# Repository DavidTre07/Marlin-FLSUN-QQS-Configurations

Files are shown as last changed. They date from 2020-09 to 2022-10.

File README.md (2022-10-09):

# 1. Marlin configuration files for FLSUN QQ-S

- [1. Marlin configuration files for FLSUN QQ-S](#1-marlin-configuration-files-for-flsun-qq-s)
  - [1.1. Purpose of this git](#11-purpose-of-this-git)
  - [1.2. How to use these files](#12-how-to-use-these-files)
  - [1.3. How to Flash](#13-how-to-flash)
  - [1.4. 1st startup after flashing a new firmware](#14-1st-startup-after-flashing-a-new-firmware)
  - [1.5. Hot End PID Tune](#15-hot-end-pid-tune)
  - [1.6. Bed PID Tune](#16-bed-pid-tune)
  - [1.7. Calibrate extruder E-Step](#17-calibrate-extruder-e-step)
  - [1.8. Level the bed](#18-level-the-bed)
  - [1.9. Calibrate dimensional print](#19-calibrate-dimensional-print)
  - [1.10. Temperature tower](#110-temperature-tower)
  - [1.11. References / Usefull Links](#111-references--usefull-links)

---

## 1.1. Purpose of this git

This is a repository for FLSUN QQ-S Marlin configuration files,  
The printer is a stock one (without mods).  
You will find also in this readme some How To for configuring / tuning your delta printer.  

---

## 1.2. How to use these files

1. Download Marlin source code (<https://marlinfw.org/>)  
2. Extract Zip file
3. Copy this repository files in the extracted Marlin zip folder  
4. Start VSCODE, install PlatformIO plugin  
5. Point VSCODE to Marlin folder  
6. Compile it !  

---

## 1.3. How to Flash

1. When compiled, copy .pio\build\mks_robin_mini\Robin_mini.bin on a MicroSD card  
2. Power off the printer
3. Insert MicroSD in the printer  
4. Power on the printer  
5. Printer will tell you the upgrade is in progress  

---

## 1.4. 1st startup after flashing a new firmware

1. Init EEPROM [*Configuration->Advanced Settings->Initialize EEPROM*]  
2. Mount the magnetic leveling switch  
3. Start Delta auto Calibration (Very long...) [*Configuration->Delta Calibration->Auto Calibration*]  
4. Heat up the hotend + Bed
5. Start Bed leveling [*Motion->Level Bed*]  
6. Now remove leveling switch  
7. Move Head to Z=0 (Be carefull, normally it will not touch the bed but you have to verify during the move)  
8. Configure Z probe offset with the paper test [*Configuration->Probe Z offset*]  
9. Save configuration in EEPROM [*Configuration->Store settings*]

---

## 1.5. Hot End PID Tune

For the following procedure I used Octoprint terminal tab:  

1. Start fan at max speed: **M106 S255**  
2. Execute auto-PID: **M303 E0 S200 C8**  
   Explanation: Hotend 0, Temp 200, 8 times  
3. Actual Firmware configuration: M301 P28.16 I3.38 D58.69  
   New value found : **M301 P16.90 I0.94 D75.85**  
   :warning: Warning: I installed a silicon protection around the heating block so don't use these values for your printer.
4. Save with : **M500**

---

## 1.6. Bed PID Tune

For the following procedure use Octoprint terminal tab:  

1. Execute auto-PID: **M303 E-1 S60 C8**  
   Explanation: Bed, Temp 60, 8 times  
2. Actual Firmware configuration: M304 P325.10 I63.35 D417.10  
   New value found: **M304 P79.68 I15.29 D276.77**
3. Save with: **M500**

---

## 1.7. Calibrate extruder E-Step

For the following procedure use Octoprint terminal tab:  

1. Remove the bowden on the extruder motor
2. Allow cold extrusion: **M302 P1**
3. Relative mode: **M83**
4. Extrude 30 cm at 500mm/min: **G1 E300 F500**
5. Check if the length is 30 cm
6. If not OK:
   - Check the current steps/mm: **M92** (Only the E value will be changed)
   - Calculate new E-Steps: *CurrentValue\*300/MesuredLength*
   - Configure the new steps/mm: **M92 E391**
   - Restart from step 3.
7. If OK then disallow cold extrusion: **M302 P0**
8. Save new value: **M500**

---

## 1.8. Level the bed

Start to check if there is a mesh, if not it will start to create a new one: **G29 V1**
Activate bed leveling : **M420 S1**
Save configuration : **M500**
Don't forget to configure you slicer to include a **M420 S1** just after **G28**

---

## 1.9. Calibrate dimensional print

Print a dice of the size of your choice.  You can found some in the stl folder.  
Recommended values of your slicer: 5% filling, speed 40mm/s.  
When done use a caliper to verify the dice size.  

If you face a difference in the size you have to adjust diagonal rod size:  

1. Print the curent configuration with: **M503**  
   Look for:  

   ```text
   Delta settings: L<diagonal rod> R<radius> H<height> S<segments per sec> XYZ<tower angle trim> ABC<rod trim>  
   M665 L280.00 R141.86 H359.31 S200.00 X-0.44 Y0.62 Z-0.18 A0.00 B0.00 C0.00
   ```

   You have to adjust *L\<diagonal rod\>*

2. Calculate the new value:  
For example if you printed a 100 mm dice but you find 99.8 mm:  
calculate the new value: *CurrentValue\*IdealSize/MesuredSize*  (280*100/99.8=280.56)  

3. Configure the new value: **M665 L280.56**

4. As you modfied the Diagonal Rod size, you have to redo:
   - Delta auto Calibration: **G33**  
   - Hot end and bed heating: **M104 S200** + **M190 S60**
   - Bed leveling: **G29**
   - Probe Z offset (paper test)
   - End of hot end and bed heating: **M104 S0; M140 S0**

Delta auto calibration + Bed leveling + ... take long time, so:

- print slowly the dice
- a small dice is nice because it print in a short time but a big dice would provide you better accuracy  
  I use a 1 cm dice for the first try then  
  2 cm dice for next adjustement  
  and finally a last 10 cm dice when close a final config (very long but accurate)  
- pay attention of the mesured size of your dice  
  (for example the first layer is usually larger so try to make mesurement without the first layer)  

---

## 1.10. Temperature tower

> TO WRITE

---

## 1.11. References / Usefull Links

|||
|:----|:---|
|Facebook group|<https://www.facebook.com/groups/120961628750040/>|
|Anders Sahlman Github|<https://github.com/AndersSahlman/Marlin>|
|Interresting Anders' post|<https://www.facebook.com/groups/120961628750040/permalink/593987384780793/>|
|Flsun QQ/QQS FAQ|<https://docs.google.com/document/d/1b_2N7NpQN2e96VPfVc_poLPOWwkM93tdAHZWOD4WEw8/edit?usp=sharing>|
|WIFI upgrade|<https://www.facebook.com/groups/120961628750040/?post_id=623723315140533><BR><https://github.com/luc-github/ESP3D>|
|Extruder calibration|<https://mattshub.com/blog/2017/04/19/extruder-calibration>|
|Calibration Hexagon|<https://www.thingiverse.com/thing:1274733>|
|Calibration Dice|<https://github.com/DavidTre07/Marlin-FLSUN-QQS-Configurations/tree/master/stl/Cube>|
|Parts for FLSUN QQS|<https://www.thingiverse.com/thing:4206957>|
|||

To Test:
|||
|:-|:-|
|Octopi Delta Micro Calibration|<https://plugins.octoprint.org/plugins/DuCalibrator>|
|||

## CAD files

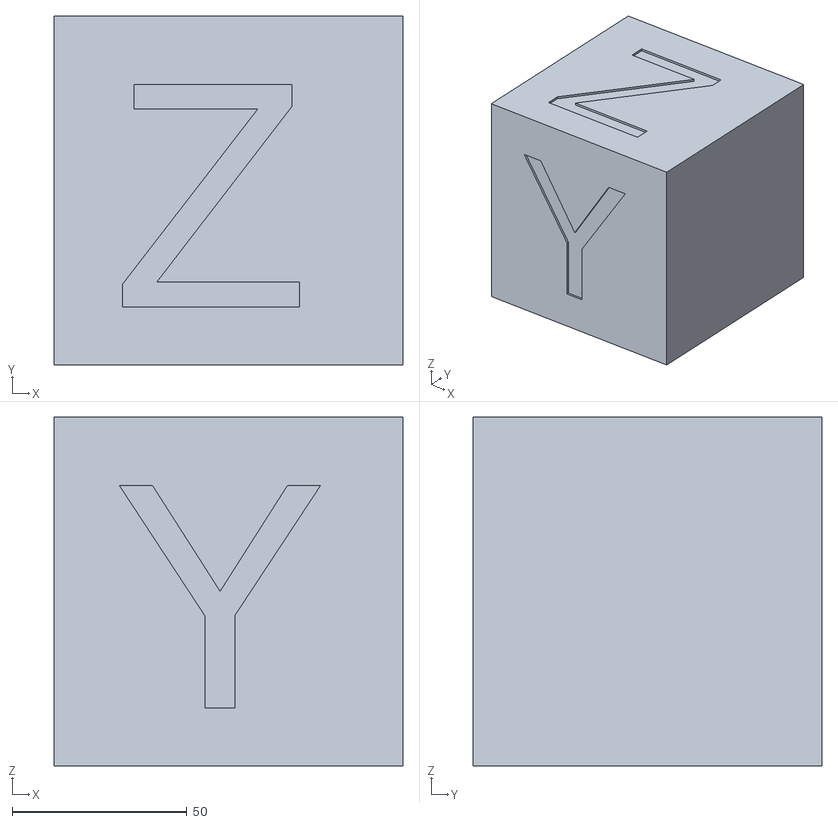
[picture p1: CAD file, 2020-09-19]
stl/Cube/100mm Calibration Cube.STL
100.0 x 100.0 x 100.0

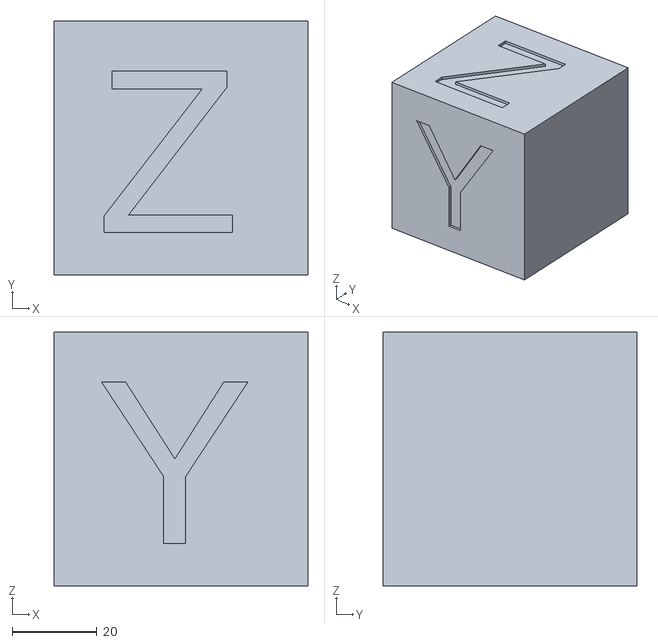
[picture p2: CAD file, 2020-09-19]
stl/Cube/60mm Calibration Cube.STL
60.0 x 60.0 x 60.0

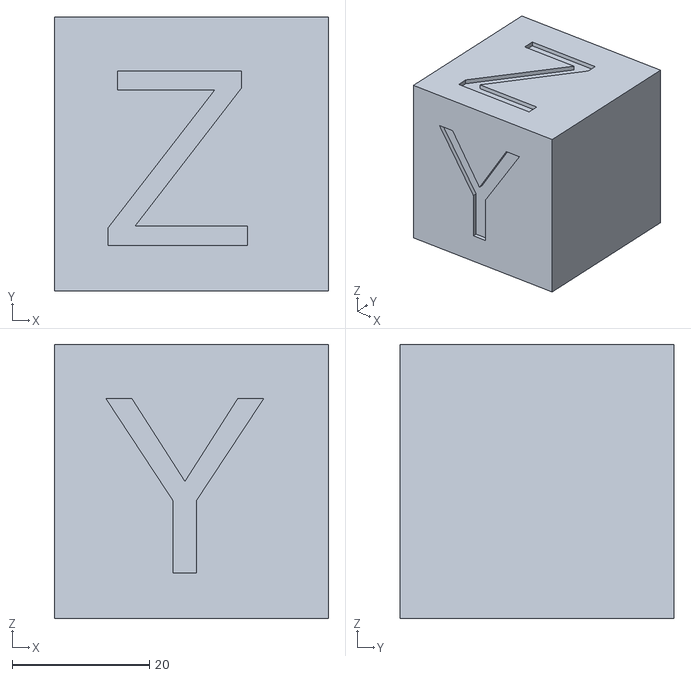
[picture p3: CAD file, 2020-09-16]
stl/Cube/40mm Calibration Cube.STL
40.0 x 40.0 x 40.0

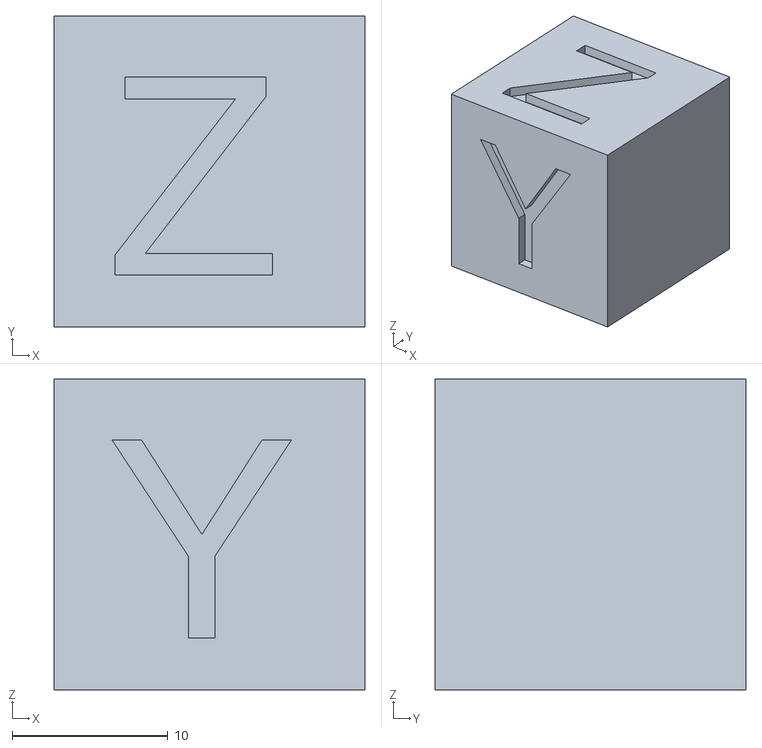
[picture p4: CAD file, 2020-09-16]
stl/Cube/20mm Calibration Cube.STL
20.0 x 20.0 x 20.0

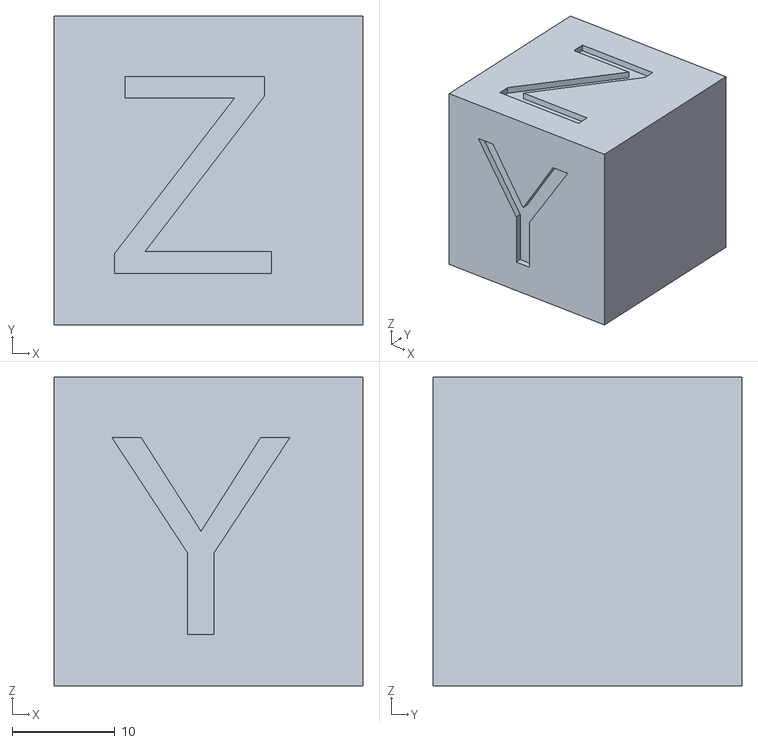
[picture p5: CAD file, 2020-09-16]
stl/Cube/30mm Calibration Cube.STL
30.0 x 30.0 x 30.0

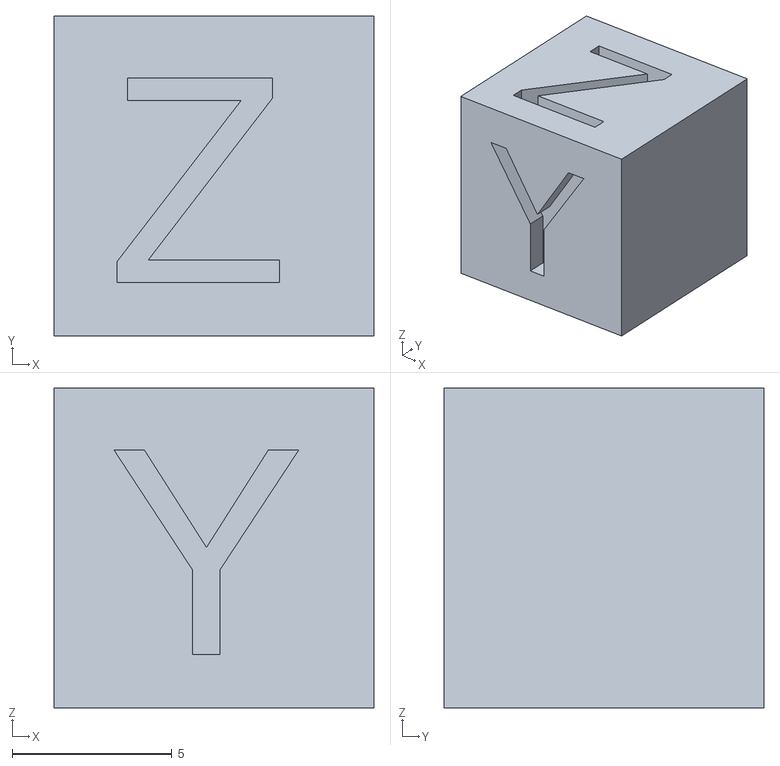
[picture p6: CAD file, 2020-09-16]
stl/Cube/10mm Calibration Cube.STL
10.0 x 10.0 x 10.0

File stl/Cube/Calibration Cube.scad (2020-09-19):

//http://github.com/DavidTre07
//Dice size in mm
size=60;

//Do not modify under this line
letterSize=size/1.5;
letterThin=1;
$fn=300;
epsilon=0.01;

difference(){
   cube(size=size);
   translate([-epsilon,(size-letterSize)/2,(size-letterSize)/2])rotate([90,0,90])
      linear_extrude(height=letterThin)text("X",size=letterSize);
   translate([(size-letterSize)/2,letterThin-epsilon,(size-letterSize)/2])rotate([90,0,0])
      linear_extrude(height=letterThin)text("Y",size=letterSize);
   translate([(size-letterSize)/2,(size-letterSize)/2,size-letterThin+epsilon])rotate([0,0,0])
      linear_extrude(height=letterThin)text("Z",size=letterSize);
}

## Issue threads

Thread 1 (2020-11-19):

Reverse display

mayalex, 2020-11-19:
Hello @DavidTre07! Perhaps, can you help me?
I used your config and got reverse display, but a touch works without reverse. (Stock Printer 2019 QQ-S)
Have been this experience?
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

Thanks!

DavidTre07, 2020-11-19:
Hello @mayalex , I don't know how to solve this issue.
I remember a old commit form Anders Sahlman on his repo about this problem but I don't know if it has been merged in Marlin.
You can check here: https://github.com/AndersSahlman/Marlin/commit/7eed139608c5388aa849a639d0142308d55b37ee
Perhaps he can drive you in the right direction.

Sorry not be very helpfull !

mayalex, 2020-11-20:
Hello @DavidTre07!
Thanks)
I solved this problem, added TFT_ROTATION with value:
`#define TFT_ROTATION TFT_ROTATE_180_MIRROR_Y`
`#define TFT_ROTATION TFT_ROTATE_180_MIRROR_X`

Closed 2020-11-20.

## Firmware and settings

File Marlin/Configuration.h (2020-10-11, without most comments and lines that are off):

#pragma once
#define CONFIG_EXAMPLES_DIR "delta/FLSUN/QQ-S"
#define CONFIGURATION_H_VERSION 020007
#define STRING_CONFIG_H_AUTHOR "(DavidTre, QQ-S config)" // Who made the changes.
#define SHOW_BOOTSCREEN
#define SERIAL_PORT 3
#define SERIAL_PORT_2 1
#define BAUDRATE 250000
  #define MOTHERBOARD BOARD_MKS_ROBIN_MINI
#define CUSTOM_MACHINE_NAME "FLSUN QQ-S"
#define EXTRUDERS 1
#define DEFAULT_NOMINAL_FILAMENT_DIA 1.75
#define TEMP_SENSOR_0 1
#define TEMP_SENSOR_1 0
#define TEMP_SENSOR_2 0
#define TEMP_SENSOR_3 0
#define TEMP_SENSOR_4 0
#define TEMP_SENSOR_5 0
#define TEMP_SENSOR_6 0
#define TEMP_SENSOR_7 0
#define TEMP_SENSOR_BED 1
#define TEMP_SENSOR_PROBE 0
#define TEMP_SENSOR_CHAMBER 0
#define DUMMY_THERMISTOR_998_VALUE 25
#define DUMMY_THERMISTOR_999_VALUE 100
#define MAX_REDUNDANT_TEMP_SENSOR_DIFF 10
#define TEMP_RESIDENCY_TIME     10  // (seconds) Time to wait for hotend to "settle" in M109
#define TEMP_WINDOW              1  // (°C) Temperature proximity for the "temperature reached" timer
#define TEMP_HYSTERESIS          3  // (°C) Temperature proximity considered "close enough" to the target
#define TEMP_BED_RESIDENCY_TIME  10 // (seconds) Time to wait for bed to "settle" in M190
#define TEMP_BED_WINDOW          1  // (°C) Temperature proximity for the "temperature reached" timer
#define TEMP_BED_HYSTERESIS      3  // (°C) Temperature proximity considered "close enough" to the target
#define HEATER_0_MINTEMP   5
#define HEATER_1_MINTEMP   5
#define HEATER_2_MINTEMP   5
#define HEATER_3_MINTEMP   5
#define HEATER_4_MINTEMP   5
#define HEATER_5_MINTEMP   5
#define HEATER_6_MINTEMP   5
#define HEATER_7_MINTEMP   5
#define BED_MINTEMP        5
#define HEATER_0_MAXTEMP 275
#define HEATER_1_MAXTEMP 275
#define HEATER_2_MAXTEMP 275
#define HEATER_3_MAXTEMP 275
#define HEATER_4_MAXTEMP 275
#define HEATER_5_MAXTEMP 275
#define HEATER_6_MAXTEMP 275
#define HEATER_7_MAXTEMP 275
#define BED_MAXTEMP      110
#define PIDTEMP
#define BANG_MAX 255     // Limits current to nozzle while in bang-bang mode; 255=full current
#define PID_MAX BANG_MAX // Limits current to nozzle while PID is active (see PID_FUNCTIONAL_RANGE below); 255=full current
#define PID_K1 0.95      // Smoothing factor within any PID loop
  #define PID_EDIT_MENU         // Add PID editing to the "Advanced Settings" menu. (~700 bytes of PROGMEM)
  #define PID_AUTOTUNE_MENU     // Add PID auto-tuning to the "Advanced Settings" menu. (~250 bytes of PROGMEM)
    #define DEFAULT_Kp  16.90
    #define DEFAULT_Ki   0.94
    #define DEFAULT_Kd  75.85
#define PIDTEMPBED
#define MAX_BED_POWER 255 // limits duty cycle to bed; 255=full current
  #define DEFAULT_bedKp 79.68
  #define DEFAULT_bedKi 15.29
  #define DEFAULT_bedKd 276.77
  #define PID_FUNCTIONAL_RANGE 15 // If the temperature difference between the target temperature and the actual temperature
#define PREVENT_COLD_EXTRUSION
#define EXTRUDE_MINTEMP 170
#define PREVENT_LENGTHY_EXTRUDE
#define EXTRUDE_MAXLENGTH 950
#define THERMAL_PROTECTION_HOTENDS // Enable thermal protection for all extruders
#define THERMAL_PROTECTION_BED     // Enable thermal protection for the heated bed
#define DELTA
  #define DELTA_SEGMENTS_PER_SECOND 200
  #define DELTA_HOME_TO_SAFE_ZONE
  #define DELTA_CALIBRATION_MENU
  #define DELTA_AUTO_CALIBRATION
    #define DELTA_CALIBRATION_DEFAULT_POINTS 7
    #define PROBE_MANUALLY_STEP 0.05      // (mm)
  #define DELTA_PRINTABLE_RADIUS 130.0    // (mm)
  #define DELTA_DIAGONAL_ROD 280.0        // (mm)
  #define DELTA_HEIGHT 372.00             // (mm) Get this value from G33 auto calibrate
  #define DELTA_ENDSTOP_ADJ { 0.0, 0.0, 0.0 } // Get these values from G33 auto calibrate
  #define DELTA_RADIUS 140.8              // (mm) Get this value from G33 auto calibrate
  #define DELTA_TOWER_ANGLE_TRIM { 0.0, 0.0, 0.0 } // Get these values from G33 auto calibrate
  #define DELTA_DIAGONAL_ROD_TRIM_TOWER { 0.0, 0.0, 0.0 }
#define USE_ZMIN_PLUG // a Z probe
#define USE_XMAX_PLUG
#define USE_YMAX_PLUG
#define USE_ZMAX_PLUG
#define ENDSTOPPULLUPS
#define X_MIN_ENDSTOP_INVERTING false  // Set to true to invert the logic of the endstop.
#define Y_MIN_ENDSTOP_INVERTING false  // Set to true to invert the logic of the endstop.
#define Z_MIN_ENDSTOP_INVERTING true  // Set to true to invert the logic of the endstop.
#define X_MAX_ENDSTOP_INVERTING false  // Set to true to invert the logic of the endstop.
#define Y_MAX_ENDSTOP_INVERTING false  // Set to true to invert the logic of the endstop.
#define Z_MAX_ENDSTOP_INVERTING false  // Set to true to invert the logic of the endstop.
#define Z_MIN_PROBE_ENDSTOP_INVERTING true  // Set to true to invert the logic of the probe.
#define X_DRIVER_TYPE  A4988
#define Y_DRIVER_TYPE  A4988
#define Z_DRIVER_TYPE  A4988
#define E0_DRIVER_TYPE A4988
#define XYZ_FULL_STEPS_PER_ROTATION 200
#define XYZ_MICROSTEPS 16
#define XYZ_BELT_PITCH 2
#define XYZ_PULLEY_TEETH 16
#define DEFAULT_XYZ_STEPS_PER_UNIT ((XYZ_FULL_STEPS_PER_ROTATION) * (XYZ_MICROSTEPS) / double(XYZ_BELT_PITCH) / double(XYZ_PULLEY_TEETH))
#define DEFAULT_AXIS_STEPS_PER_UNIT   { DEFAULT_XYZ_STEPS_PER_UNIT, DEFAULT_XYZ_STEPS_PER_UNIT, DEFAULT_XYZ_STEPS_PER_UNIT, 393 }  // default steps per unit
#define DEFAULT_MAX_FEEDRATE          { 200, 200, 200, 200 }
#define DEFAULT_MAX_ACCELERATION      { 1000, 1000, 1000, 1000 }
#define LIMITED_MAX_ACCEL_EDITING     // Limit edit via M201 or LCD to DEFAULT_MAX_ACCELERATION * 2
  #define MAX_ACCEL_EDIT_VALUES       { 6000, 6000, 6000, 20000 } // ...or, set your own edit limits
#define DEFAULT_ACCELERATION          1000    // X, Y, Z and E acceleration for printing moves
#define DEFAULT_RETRACT_ACCELERATION  1000    // E acceleration for retracts
#define DEFAULT_TRAVEL_ACCELERATION   1000    // X, Y, Z acceleration for travel (non printing) moves
#define CLASSIC_JERK
  #define DEFAULT_XJERK 10.0
  #define DEFAULT_YJERK DEFAULT_XJERK
  #define DEFAULT_ZJERK DEFAULT_XJERK // Must be same as XY for delta
  #define LIMITED_JERK_EDITING        // Limit edit via M205 or LCD to DEFAULT_aJERK * 2
    #define MAX_JERK_EDIT_VALUES { 20, 20, 20, 10 } // ...or, set your own edit limits
#define DEFAULT_EJERK    5.0  // May be used by Linear Advance
#define S_CURVE_ACCELERATION
#define Z_MIN_PROBE_USES_Z_MIN_ENDSTOP_PIN
#define FIX_MOUNTED_PROBE
#define NOZZLE_TO_PROBE_OFFSET { 0, 0, -16.22 }  //size of the magnetic sensor
#define PROBING_MARGIN 20
#define XY_PROBE_SPEED (66*60)
#define Z_PROBE_SPEED_FAST HOMING_FEEDRATE_Z
#define Z_PROBE_SPEED_SLOW (Z_PROBE_SPEED_FAST / 10)
#define MULTIPLE_PROBING 3
#define EXTRA_PROBING    1
#define Z_CLEARANCE_DEPLOY_PROBE   30 // Z Clearance for Deploy/Stow
#define Z_CLEARANCE_BETWEEN_PROBES  5 // Z Clearance between probe points
#define Z_CLEARANCE_MULTI_PROBE     5 // Z Clearance between multiple probes
#define Z_AFTER_PROBING            30 // Z position after probing is done
#define Z_PROBE_LOW_POINT          -2 // Farthest distance below the trigger-point to go before stopping
#define Z_PROBE_OFFSET_RANGE_MIN -20
#define Z_PROBE_OFFSET_RANGE_MAX 20
#define Z_MIN_PROBE_REPEATABILITY_TEST
#define PAUSE_BEFORE_DEPLOY_STOW
#define PROBING_FANS_OFF          // Turn fans off when probing
#define DELAY_BEFORE_PROBING 200  // (ms) To prevent vibrations from triggering piezo sensors
#define X_ENABLE_ON 0
#define Y_ENABLE_ON 0
#define Z_ENABLE_ON 0
#define E_ENABLE_ON 0 // For all extruders
#define DISABLE_X false
#define DISABLE_Y false
#define DISABLE_Z false
#define DISABLE_E false             // Disable the extruder when not stepping
#define DISABLE_INACTIVE_EXTRUDER   // Keep only the active extruder enabled
#define INVERT_X_DIR false
#define INVERT_Y_DIR false
#define INVERT_Z_DIR false
#define INVERT_E0_DIR true
#define INVERT_E1_DIR false
#define INVERT_E2_DIR false
#define INVERT_E3_DIR false
#define INVERT_E4_DIR false
#define INVERT_E5_DIR false
#define INVERT_E6_DIR false
#define INVERT_E7_DIR false
#define NO_MOTION_BEFORE_HOMING // Inhibit movement until all axes have been homed
#define X_HOME_DIR 1  // deltas always home to max
#define Y_HOME_DIR 1
#define Z_HOME_DIR 1
#define X_BED_SIZE ((DELTA_PRINTABLE_RADIUS) * 2)
#define Y_BED_SIZE ((DELTA_PRINTABLE_RADIUS) * 2)
#define X_MIN_POS -(DELTA_PRINTABLE_RADIUS)
#define Y_MIN_POS -(DELTA_PRINTABLE_RADIUS)
#define Z_MIN_POS 0
#define X_MAX_POS DELTA_PRINTABLE_RADIUS
#define Y_MAX_POS DELTA_PRINTABLE_RADIUS
#define Z_MAX_POS MANUAL_Z_HOME_POS
#define MIN_SOFTWARE_ENDSTOPS
  #define MIN_SOFTWARE_ENDSTOP_X
  #define MIN_SOFTWARE_ENDSTOP_Y
  #define MIN_SOFTWARE_ENDSTOP_Z
#define MAX_SOFTWARE_ENDSTOPS
  #define MAX_SOFTWARE_ENDSTOP_X
  #define MAX_SOFTWARE_ENDSTOP_Y
  #define MAX_SOFTWARE_ENDSTOP_Z
  #define SOFT_ENDSTOPS_MENU_ITEM  // Enable/Disable software endstops from the LCD
#define AUTO_BED_LEVELING_BILINEAR
#define RESTORE_LEVELING_AFTER_G28
  #define SEGMENT_LEVELED_MOVES
  #define LEVELED_SEGMENT_LENGTH 5.0 // (mm) Length of all segments (except the last one)
  #define G26_MESH_VALIDATION
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

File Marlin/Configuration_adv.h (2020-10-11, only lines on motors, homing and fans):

#define E0_AUTO_FAN_PIN -1
#define E1_AUTO_FAN_PIN -1
#define E2_AUTO_FAN_PIN -1
#define E3_AUTO_FAN_PIN -1
#define E4_AUTO_FAN_PIN -1
#define E5_AUTO_FAN_PIN -1
#define E6_AUTO_FAN_PIN -1
#define E7_AUTO_FAN_PIN -1
#define CHAMBER_AUTO_FAN_PIN -1
#define HOMING_BUMP_MM      { 5, 5, 5 }       // (mm) Backoff from endstops after first bump
#define HOMING_BUMP_DIVISOR { 10, 10, 10 }       // Re-Bump Speed Divisor (Divides the Homing Feedrate)
#define MICROSTEP_MODES { 16, 16, 16, 16, 16, 16 } // [1,2,4,8,16]
#define ADVANCED_PAUSE_FEATURE
  #define ADVANCED_PAUSE_CONTINUOUS_PURGE         // Purge continuously up to the purge length until interrupted.
  #define ADVANCED_PAUSE_PURGE_FEEDRATE        3  // (mm/s) Extrude feedrate (after loading). Should be slower than load feedrate.
  #define ADVANCED_PAUSE_PURGE_LENGTH        150  // (mm) Length to extrude after loading.
  #define ADVANCED_PAUSE_RESUME_PRIME          0  // (mm) Extra distance to prime nozzle after returning from park.
  #define HOME_BEFORE_FILAMENT_CHANGE           // If needed, home before parking for filament change

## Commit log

2020-09-05 Initial commit as of official 2.0.6.1
    [Configuration.h, Configuration_adv.h]
2020-09-05 Multiple changes
    [Configuration.h, Configuration_adv.h]
2020-09-07 Removed GFX OVERLAY+Added sensors size+new display
    [Configuration.h, Configuration_adv.h]
2020-09-13 Added PID Tune
2020-09-16 Dimensional print How To
    [10mm Calibration Cube.STL, 20mm Calibration Cube.STL, 30mm Calibration Cube.STL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]
2020-09-19 Calibrate dimensional
    [100mm Calibration Cube.STL, 60mm Calibration Cube.STL, Calibration Cube.scad]
2020-09-23 Small corrections
    [Configuration_adv.h]
2020-09-30 Host communication activ (future filament sensor)
    [Configuration.h, Configuration_adv.h]
2020-10-11 PID temp adjusted
    [Configuration.h]
2022-10-09 Add bed leveling

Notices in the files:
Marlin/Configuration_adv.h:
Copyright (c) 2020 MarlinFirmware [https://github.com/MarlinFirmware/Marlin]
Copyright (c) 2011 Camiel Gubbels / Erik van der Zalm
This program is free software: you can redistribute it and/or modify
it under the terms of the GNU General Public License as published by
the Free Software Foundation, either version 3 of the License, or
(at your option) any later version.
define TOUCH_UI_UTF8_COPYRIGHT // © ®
